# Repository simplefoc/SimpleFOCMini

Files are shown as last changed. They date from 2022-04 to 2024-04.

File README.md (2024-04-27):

# SimpleFOCMini v1.1

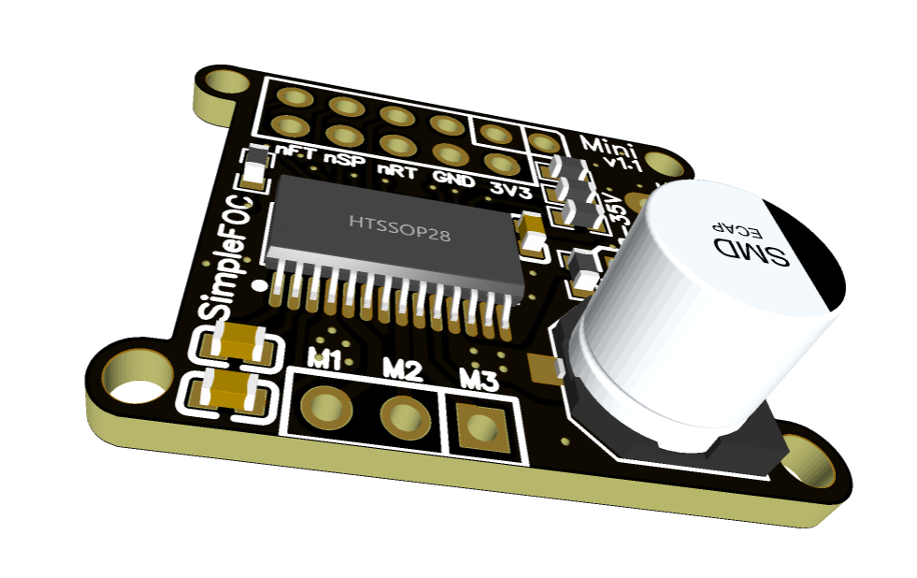
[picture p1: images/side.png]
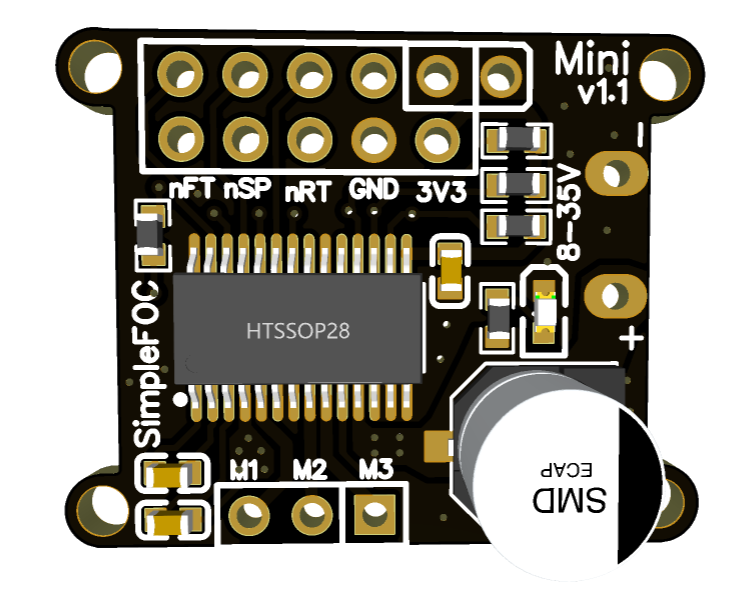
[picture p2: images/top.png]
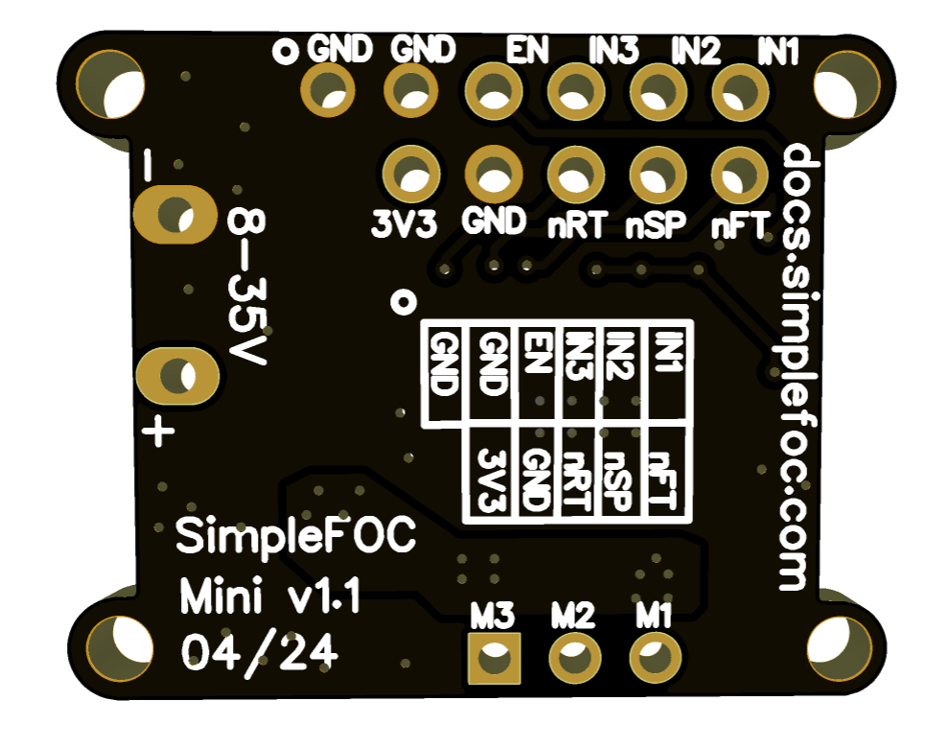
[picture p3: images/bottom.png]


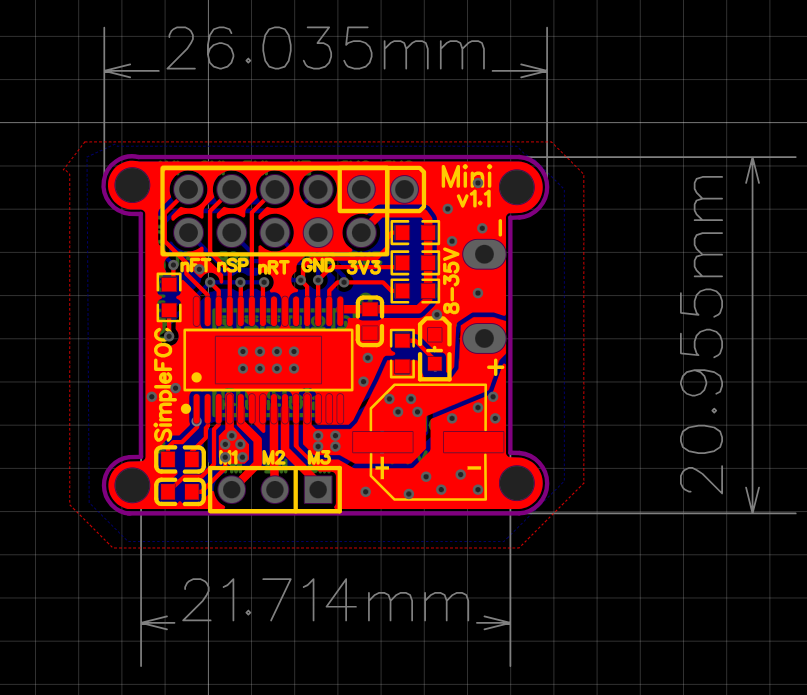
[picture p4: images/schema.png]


## Features
- DRV8313 based - [datasheet](https://www.ti.com/lit/ds/symlink/drv8313.pdf?ts=1650461862269&ref_url=https%253A%252F%252Fwww.google.com%252F)
  - Power supply: 8-24V
  - Max current: 2.5A per phase
  - Onboard 3.3V LDO
- Small size 26x21 mm
- Fully compatible with the *Simple**FOC**library*
- Fully open-source: [EasyEDA link](https://easyeda.com/the.skuric/simplefocmini)
- Low-cost: JLCPCB production cost ~3-5€
- Available in the [shop](https://www.simplefoc.com/shop) 10-15€ 

## New features in v1.1
- Aligned motor output header with the input header so that it can be stacked in the protoboard
- Input header updated to be easier to use with arduino UNO, nucleos, but also with qtpy...
  - Changed the order of the IN1,IN2,IN3 and EN: 
  - Added an additional GND pin 
- First batch of the SimpleFOCMini V1.1 will be available in the [shop](https://www.simplefoc.com/shop) soon: Price: 10-15€ 

## Getting started with SimpleFOCMini

See the documentation in the [SimpleFOC documentation](https://docs.simplefoc.com/simplefocmini) page. 
- The docs explain how to start with the SimpleFOCMini board and how to use it with the SimpleFOC library. 
- They also describe how you can order it directly from the JLCPCB.

## Release log

Release | Date | Description
--- | --- | ---
v1.1 | 2024-04 | A quick iteration with a few changes: <p> 1. Aligned motor output header with the input header so that it can be stacked in the protoboard<br>2. Input header updated to be easier to use with arduino UNO, nucleos, but also with qtpy...<br> - Changed the order of the IN1,IN2,IN3 and EN: <br>    - Added an additional GND pin <br>
v1.0 | 2022-04 | Initial release

## Size comparison



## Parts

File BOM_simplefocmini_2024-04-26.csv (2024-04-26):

ID | Name | Designator | Footprint | Quantity | Manufacturer Part | Manufacturer | Supplier | Supplier Part | Price
1 | 19-213/Y2C-CQ2R2L/3T(CY) | LED1 | LED0603-R-RD | 1 | 19-213/Y2C-CQ2R2L/3T(CY) | EVERLIGHT | LCSC | C72038 | 0.019
2 | 1kΩ | R5 | R0603 | 1 | 0603WAF4701T5E | UniOhm | LCSC | C23162 | 0.001
3 | 100uF | C3 | CAP-SMD_BD6.3-L6.6-W6.6-FD | 1 | VT1V101M-CRE77 | Vertical Technology | LCSC | C294520 | 0.032
4 | 10kΩ | R1,R2,R3,R4 | R0603 | 4 | 0603WAF4701T5E | UniOhm | LCSC | C23162 | 0.001
5 | 100nF | C1,C2 | C0603 | 2 | CL10B104KB8NNNC | SAMSUNG | LCSC | C1591 | 0.002
6 | 470nF | C4 | C0603 | 1 | CC0603ZRY5V6BB474 | YAGEO | LCSC | C327269 | 0.008
7 | DRV8313PWPR | U1 | HTSSOP-28_L9.8-W4.5-P0.65-LS6.6-BL-EP | 1 | DRV8313PWPR | Texas Instruments | LCSC | C92482 | 2.189

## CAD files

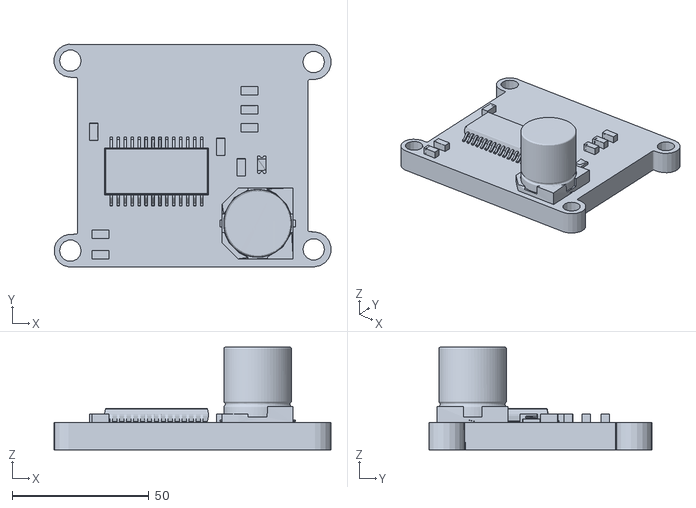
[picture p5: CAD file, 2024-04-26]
3D model/OBJ_simplefocmini.obj
101.3 x 81.4 x 37.6

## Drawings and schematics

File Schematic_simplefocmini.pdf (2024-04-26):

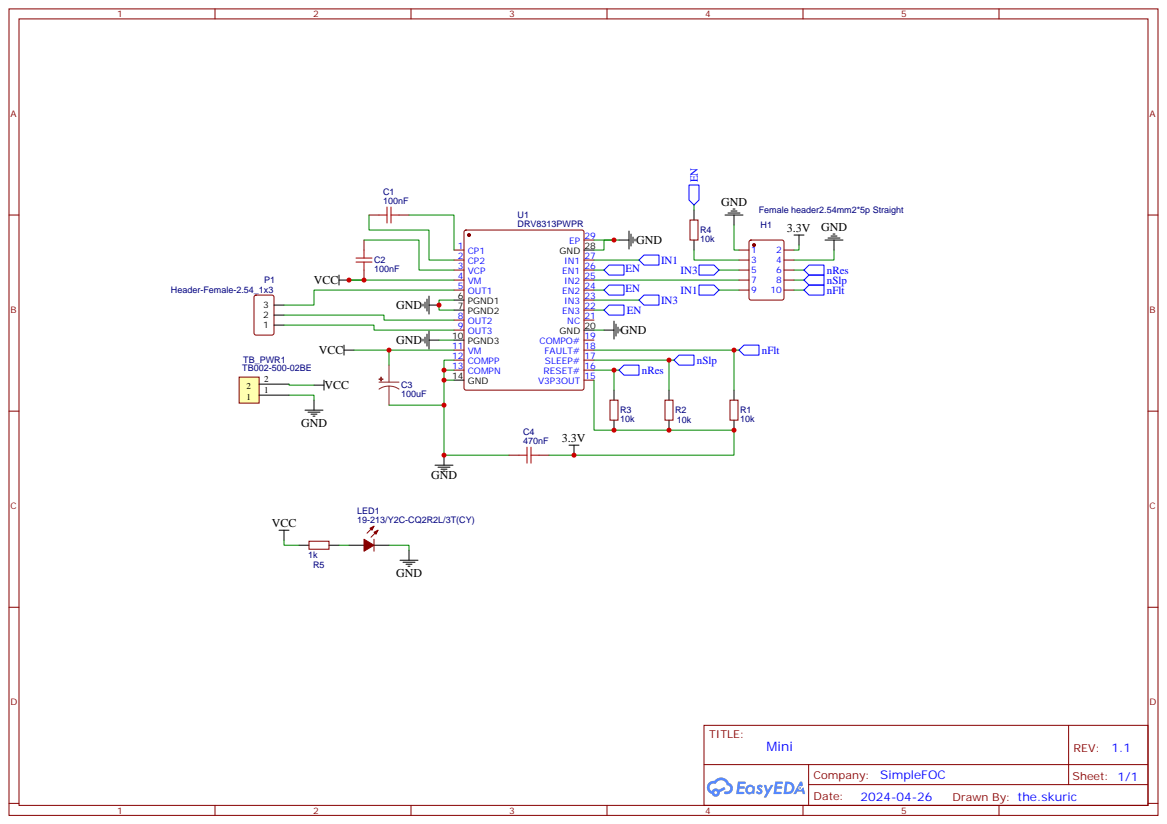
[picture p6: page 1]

Drawn By: the.skuric

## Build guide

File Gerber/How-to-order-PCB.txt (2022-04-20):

How to Order PCB

Please refer to:
https://docs.easyeda.com/en/PCB/Order-PCB

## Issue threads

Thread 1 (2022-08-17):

When will this be in store?

harryloud, 2022-08-17:
This board is perfect for our use case.
I would love to buy it.
When will it be availiable?

askuric, 2022-10-15:
SimpleFOCMini is available in the shop. :D

Closed 2022-10-15.

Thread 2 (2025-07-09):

En pin pulldown.

rewolff, 2025-07-09:
According to Antun_Skuric on the forum the resistor connected to the EN pin was meant to be a pulldown and not a series resistor.

And IMHO that makes very much sense. (I now own 60 bad PCBs...)

I don't know if maybe this was "fixed" in the altium files, but the PDF schematic is lagging, but the PDF shows a series resistor, so at least the PDF should be upgraded.

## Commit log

2022-04-20 initial upload
    [Drill_PTH_Through.DRL, Gerber_BoardOutlineLayer.GKO, Gerber_BottomLayer.GBL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]
2024-04-26 v1.1 revision
    [BOM_simplefocmini_2024-04-26.csv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]
2024-04-26 the update for the v1.1
    [BOM_simplefocmini_2024-04-26.csv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]
